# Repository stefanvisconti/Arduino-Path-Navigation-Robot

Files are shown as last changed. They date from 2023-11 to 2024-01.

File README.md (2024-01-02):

# SIngle-Actuator-Arduino-Path-Navigation-Robot
Wheeled Mobile Robot controlled with an Arduino UNO to navigate through pre-determined paths, and around obstacles. A figure of the robot design can be seen below.



The goal of this project is to gain hands-on experience with microcontrollers, sensors, actuators and the programming required to interface with them. The robot is designed to complete four distinct tasks wherein it must: navigate through HMI, navigate autonomously and avoid objects. The solution created was a single actuator design that is able to turn and move forward/backward using one motor on a pivoting ratchet. The robot is able to determine  position using ultrasonic sensors and using these will navigate the tasks accordingly. There are many constraints on this project such as: time, funds and resources which increased the difficulty in creating a solution. In this experiment the design process including: problem definition, solution formulation, modelling, prototyping and implementation will be explored in order to gain in-depth hands-on experience with mechatronics topics.

A video of the system performing in it's manual control option is shown below.

https://drive.google.com/file/d/11_2gsuO4MDafjLckb3ffVChpPL_l2O8q/view?usp=drive_link

## List of Materials

In order to construct the physical mechanism to be used for this project, mostly 3D printed parts were used for structural elements. The single actuator used is the N20 Motor which was already owned by a group member. The paper clips, copper tubing, and o-rings were scrap materials found at home. All of the remaining electrical parts have been taken from the Elegoo Starter Kit. However, a complete list of the costs were considered if each component needed to be purchased. A comprehensive list of all of the hardware that has been used in this project is given in the table below.

<table>
  <tr>
    <th>Name</th>
    <th>Description</th>
    <th>Quantity</th>
    <th>Unit Cost</th>
    <th>Cost</th>
  </tr>
  <tr>
    <td>Main Body Back</td>
    <td>3D Printed</td>
    <td>1</td>
    <td>$0</td>
    <td>$0</td>
  </tr>
  <tr>
    <td>Back Deck</td>
    <td>3D Printed</td>
    <td>1</td>
    <td>$0</td>
    <td>$0</td>
  </tr>
  <tr>
    <td>Back Wheel</td>
    <td>3D Printed</td>
    <td>2</td>
    <td>$0</td>
    <td>$0</td>
  </tr>
  <tr>
    <td>Back Wheel Axle</td>
    <td>3D Printed</td>
    <td>2</td>
    <td>$0</td>
    <td>$0</td>
  </tr>
  <tr>
    <td>Ring Gear Plate</td>
    <td>3D Printed</td>
    <td>1</td>
    <td>$0</td>
    <td>$0</td>
  </tr>
  <tr>
    <td>Main Pivot</td>
    <td>3D Printed</td>
    <td>1</td>
    <td>$0</td>
    <td>$0</td>
  </tr>
  <tr>
    <td>Motor Frame</td>
    <td>3D Printed</td>
    <td>1</td>
    <td>$0</td>
    <td>$0</td>
  </tr>
  <tr>
    <td>Main Wheel Gear</td>
    <td>3D Printed</td>
    <td>1</td>
    <td>$0</td>
    <td>$0</td>
  </tr>
  <tr>
    <td>Idler Gear</td>
    <td>3D Printed</td>
    <td>1</td>
    <td>$0</td>
    <td>$0</td>
  </tr>
  <tr>
    <td>Spur Gear</td>
    <td>3D Printed</td>
    <td>1</td>
    <td>$0</td>
    <td>$0</td>
  </tr>
  <tr>
    <td>Motor Gear</td>
    <td>3D Printed</td>
    <td>1</td>
    <td>$0</td>
    <td>$0</td>
  </tr>
  <tr>
    <td>Bevel Gear</td>
    <td>3D Printed</td>
    <td>1</td>
    <td>$0</td>
    <td>$0</td>
  </tr>
  <tr>
    <td>Bevel Spur Gear</td>
    <td>3D Printed</td>
    <td>1</td>
    <td>$0</td>
    <td>$0</td>
  </tr>
  <tr>
    <td>Idler</td>
    <td>3D Printed</td>
    <td>1</td>
    <td>$0</td>
    <td>$0</td>
  </tr>
  <tr>
    <td>Pivot Cap</td>
    <td>3D Printed</td>
    <td>1</td>
    <td>$0</td>
    <td>$0</td>
  </tr>
  <tr>
    <td>Brush Mount</td>
    <td>3D Printed</td>
    <td>1</td>
    <td>$0</td>
    <td>$0</td>
  </tr>
  <tr>
    <td>Brush Mount Clamp</td>
    <td>3D Printed</td>
    <td>1</td>
    <td>$0</td>
    <td>$0</td>
  </tr>
  <tr>
    <td>Elegoo UNO R3</td>
    <td>Elegoo Starter Kit</td>
    <td>1</td>
    <td>$23.99</td>
    <td>$23.99</td>
  </tr>
  <tr>
    <td>L298N Motor Driver</td>
    <td>Elegoo Starter Kit</td>
    <td>1</td>
    <td>$3.95</td>
    <td>$3.95</td>
  </tr>
  <tr>
    <td>MPU6050 IMU Sensor</td>
    <td>Elegoo Starter Kit</td>
    <td>1</td>
    <td>$7.50</td>
    <td>$7.50</td>
  </tr>
  <tr>
    <td>HC-SR04 Ultrasonic Sensor</td>
    <td>Elegoo Starter Kit</td>
    <td>2</td>
    <td>$4.50</td>
    <td>$9.00</td>
  </tr>
  <tr>
    <td>N20 DC Motor</td>
    <td>Elegoo Starter Kit</td>
    <td>1</td>
    <td>$7.99</td>
    <td>$7.99</td>
  </tr>
  <tr>
    <td>Copper Tubing</td>
    <td>Scrap Material</td>
    <td>1</td>
    <td>$1.20</td>
    <td>$1.20</td>
  </tr>
  <tr>
    <td>Paper Clip</td>
    <td>Scrap Material</td>
    <td>2</td>
    <td>$0.10</td>
    <td>$0.20</td>
  </tr>
  <tr>
    <td>O-Ring</td>
    <td>Scrap Material</td>
    <td>4</td>
    <td>$1.36</td>
    <td>$5.44</td>
  </tr>
  <tr>
    <td>9V Battery</td>
    <td>Elegoo Starter Kit</td>
    <td>1</td>
    <td>$4.50</td>
    <td>$4.50</td>
  </tr>
  <tr>
    <td>Spring</td>
    <td>Scrap Material</td>
    <td>1</td>
    <td>$1.20</td>
    <td>$1.20</td>
  </tr>
  <tr>
    <td>4x3/4 Countersink Screw</td>
    <td>Scrap Material</td>
    <td>6</td>
    <td>$0.67</td>
    <td>$4.00</td>
  </tr>
  <tr>
    <td>M3 Screw</td>
    <td>Scrap Material</td>
    <td>4</td>
    <td>$0.60</td>
    <td>$2.40</td>
  </tr>
  <tr>
    <td>Wire</td>
    <td>Elegoo Starter Kit</td>
    <td>23</td>
    <td>$0.56</td>
    <td>$12.99</td>
  </tr>
  <tr>
    <td>PKCELL 9V Battery Connector</td>
    <td>Elegoo Starter Kit</td>
    <td>1</td>
    <td>$5.33</td>
    <td>$5.33</td>
  </tr>
  <tr>
    <td>Total Cost</td>
    <td></td>
    <td></td>
    <td></td>
    <td>$89.69</td>
  </tr>
</table>

## Schematic and Technical Design Details of Electronics

A circuit diagram of this hardware setup can be seen below. This is created digitally using the TinkerCAD software offered by Autodesk. The diagram is a simplified representation of the wiring setup, where the components are shown graphically. 



However, if a more accurate-to-real-life circuit diagram is desired, an alternative modelling software must be used. The electrical wiring schematic developed using KiCAD can be seen in the figure below. This circuit provides more accuracy, allowing the circuit to be modelled more accurately to the real life thing.



In the figure above, the MPU-6050 symbol is the MPU6050 IMU Sensor board, and the L298N symbol is the L298N Motor Driver board. The Motor_DC symbol is the DC motor being used to drive the gearbox. The two HC-SR04 symbols are the two ultrasonic sensors used for obstacle avoidance in task 3. Finally, the AnalogJoystick1 symbol is the joystick module used to manually control the device. Additionally, the Arduino_UNO_R3 module represents the Elegoo UNO R3 board.

## CAD Models and Technical Design Details of Mechanics

The physical design of this system is quite intricate given the single actuator used to drive the system. Due to this stipulation, certain design considerations must be taken in order to achieve this goal. Additionally, the car was to be constructed using only available materials, and no parts were to be purchased, implying that the cost of the car would be $0. This resulted in almost all of the parts of the device being 3D printed.

The main form of the device is a car with 3 wheels. The two wheels at the back of the car are idler wheels, and are simply there to provide support to the vehicle while it drives. The wheel in the front is the driving wheel, which is fitted with a gearbox and a motor. The front wheel will be able to drive the car forward, as well as rotate to act like a pivot. This is how the car will be able to steer.
The entire mechanism assembly can be seen below, modelled using the online CAD software, Onshape.



The assembly consists of a number of parts. These include the motor, Elegoo UNO R3 board, spring, ultrasonic sensors, o-rings, and all of the 3D printed parts. The 3D printed parts make up the large majority of the assembly. These include, the main body, back deck, back wheel, back wheel axle, ring gear plate, main pivot, motor frame, main wheel gear, idler gear, spur gear, motor gear, bevel gear, bevel spur gear, idler, pivot cap, brush mount, brush mount clamp, ultrasonic sensor mount, and ultrasonic sensor mount mount.

To start, the main body is the largest part of the assembly, all other parts connect to this. It features two cutouts on the side with a threaded hole for the back wheel axle to screw into. It also has the back of the body hollowed out with slots for the back deck to slide into. It also has a circular cutout on the front with screw holes for the ring gear plate with screw holes to screw into. A screenshot of the CAD model of this is shown below.



Sliding into the main body is the back deck. This features a plate for the Elegoo UNO R3 board to screw into. Underneath the back deck is where the L298N motor driver is housed. A screenshot of the CAD model of this is shown below.



Again, attaching to the main body are the back wheel axles. There are two of these and they are fitted with threaded rods that will allow them to screw into the main body. A screenshot of the CAD model of this is shown below.



Accompanying the back wheel axle is the back wheel. This is what provides stability to the rear of the car. They have grooves along the circumference of the wheel in which a plumbing o-ring is able to fit around. This provides the friction needed to be able to spin on the floor. A screenshot of the CAD model of this is shown below.



Another large part of the assembly is the ring gear plate. This screws into the front of the main body and features a large ring gear which will allow the front wheel to pivot around. A screenshot of the CAD model of this is shown below.



The Elegoo UNO R3 board is the main brains of the device. This controls the motor speed and direction and reads and processes values from the sensors. A screenshot of the CAD model of this is shown below.



Sliding through the top of the ring gear plate is the main pivot. This part will be rotating with the main wheel. It is fastened to the ring gear using a set of nuts. The main pivot will also have a hole cut through the middle of it to allow the wires from the motor to be snaked through to be accessible by the arduino. Additionally, with the wires, the pivot will support two pieces of brass tubing which will be used as commutator wings. The wires will be soldered to these and have brushes (paperclips) which will allow power to be supplied to the motor without having the wires get tangled as it rotates. A screenshot of the CAD model of this is shown below.



The brushes, which in this case are paper clips, will be fastened to the device using the brush mounts. These will be screwed into the ring gear plate, and will act as a clamp on the paper clips. One end of the paper clip will be brushing the commutator rings, and the other end will be soldered to a wire which is connected to the L298N motor driver. A screenshot of the CAD model of these are shown below.



Attached to the main pivot is the motor frame. This is quite the complex part as it will the motor and all of the gears which will allow the single actuator steering mechanism to work. A screenshot of the CAD model of this is shown below.



The main wheel of the car features a 38 tooth gear which will be driven by the gearbox on the motor frame. Similarly to the back wheel, it will also have two plumbing o-rings around it which will provide the friction needed for it to drive on the floor. A screenshot of the CAD model of this is shown below.



Next are the rest of the gears. The majority of these look quite similar. A screenshot of the CAD model of all of these are shown below.



Accompanying the gears is the idler. This is the main part that will allow for the single actuator steering mechanism to work. It allows the idler gear to switch between meshing with the main wheel gear and meshing with the pivot mechanism. When the motor changes direction, a spring pushing on the idler allows the idler to switch between driving mechanisms. However, it applies just enough force to allow the idler to move but not enough for the motor gear to be prevented from turning. A screenshot of the CAD model of this is shown below.



A screenshot of the overall driving mechanism can be seen below.



The sensing of the device is done using ultrasonic sensors which are mounted to the front of the car. This sensor mount comes in two pieces. One large piece which will attach onto the ring gear plate, and another which will hold the ultrasonic sensor. These two pieces will screw into each other. It was decided that the necessary distance between each sensor would be 3 inches. A screenshot of the CAD model of these are shown below.



## Controller Design and Block Diagram of Control System

The control system of this project is designed based on the mathematical modelling and simulation previously done. This was the result of the inverse kinematics problem, and the Simulink simulation of the system. From the equations developed in that section, the block diagram for the control system can be created. The controller itself will be described by a transfer function which will be created from the equations previously obtained.
The control system for this project can be described using the following block diagram shown below.



The Ts block represents the transfer function developed in the Mathematical Modelling section. The vRs block represents the desired robot velocity, s represents the wheel angular velocities, t represents the current angle of the robot. The controller takes in the desired velocity of the robot, and outputs the corresponding wheel angular velocities that will achieve that velocity.

## Flowchart and Description of the Software Program

The flowcharts that describe the Arduino scripts can be found in the following figures. All scripts begin by including the necessary libraries, assigning respective pins for sensors and motor, defining all required variables and setting the pin modes. For manual control, the void loop() consists of reading the joystick data and mapping the joystick position to motor speed. That is, for the joystick range of 0 to 1023, the motor speed is mapped from -255 to 255. If the joystick is in the forward position (i.e, positive motor speed), then the motor drives the robot forward. Simularily, if the joystick is in the backward direction (i.e., negative motor speed), then the motor is reversed resulting in the rotation of the steering shaft. If neither statement is true, then the motor stops and the robot does not move. The flowchart for manual control can be seen below. 



For autonomous path navigation, the void loop() begins by reading the ultrasonic and MPU data. The ultrasonic is used to detect the distance of objects ahead, while the MPU measures the rotation of the steering shaft such that the exact direction is known. If the robot is not close to an object, then the robot continues moving forward. If the robot is close to the first object, then the robot turn right 90-degrees. If the robot is close to the second object, then the robot turns left 90-degrees. If the robot senses an object, but it is neither the first or the second, then the robot is at the final object and motion is stopped. The flowchart for autonomous path navigation can be seen below. 



For obstacle avoidance, the void loop() begins by reading the ultrasonic and MPU data. If the robot is not close to an object, then the robot continues moving forward. If the robot is close to the object, then an avoidance deviation sequence is initiated. That is, the robot turns right and travels forward for X seconds until the object is clear. Then the robot turns left and goes forward for X seconds to get past the object. The robot then turns left again and goes forward for X seconds to reach the original path. Another right turn is executed to face the robot towards the finish line. The robot then travels forward for X seconds until the robot reaches the finish line. The flowchart for obstacle avoidance can be seen below. 



Simularily, for the accuracy test, the void loop() begins by reading the ultrasonic and MPU data. If the robot is not close to an object, then the robot continues moving forward. Each time the robot get close to an object it turns right and continues forward. If the senses object is the forth object, then the script ends. The flowchart for the accuracy test can be seen in the figure below. 



## Conclusions and Recommendations

Overall the robotic system that was created was able to be both mechanically innovative and realistically feasible with its execution of the tasks as detailed by the project addendum. Fundamental design formulas were followed during the conceptualization of the solution put forth in this project. These involved strong project initialization exercises such as mind maps, clearly defined functional, constraints and characteristics, and black box diagrams to be used when coming to the formulation of the design. This came to fruition as a one actuated geared robotic drive system that would be able to drive and pivot with two degrees of freedom. The design was easy to drive and provided comparatively little error as opposed to robots with more actuators. To begin the design process of this both mathematical and simulated models were created to test the feasibility of the design. Afterwards, detailed CADs were created to make a model that was almost completely 3D printed. This had the added benefit of keeping the cost of the robots to 0$ which was another one of the ancillary goals of the project detail. 

To control the robot, Arduino along with an ultrasonic sensor, and MPU 6050 was used to both determine any obstacles or the position of the robot. The MPU was especially important for the bearing of the pivot along with the rotation of the body of the drone. In addition, the motion of the robot was mathematically modelled using inverse kinematics. A transfer function was developed such that the controller takes in the desired velocity of the robot, and outputs the corresponding wheel angular velocities that will achieve that velocity.

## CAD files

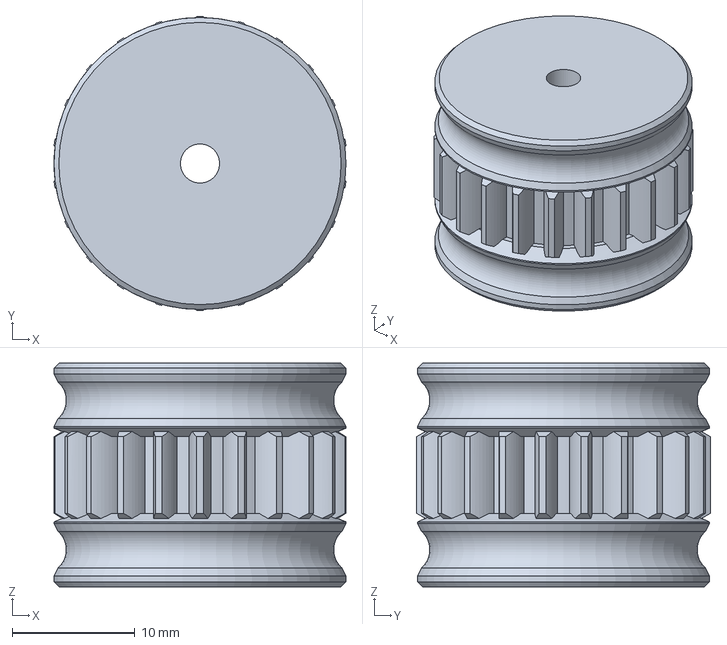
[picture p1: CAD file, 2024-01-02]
CAD Models/Main Wheel Gear.step
23.8 x 24.0 x 18.3 mm

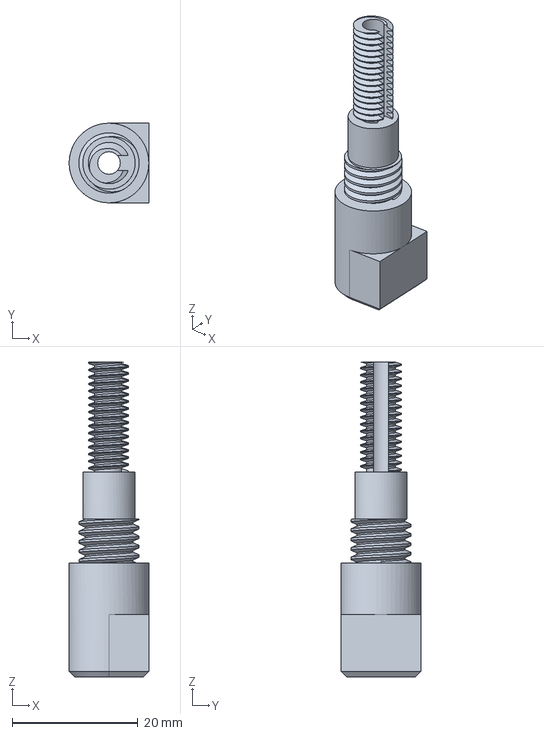
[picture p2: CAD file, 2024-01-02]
CAD Models/Main Pivot.step
12.7 x 12.7 x 50.2 mm

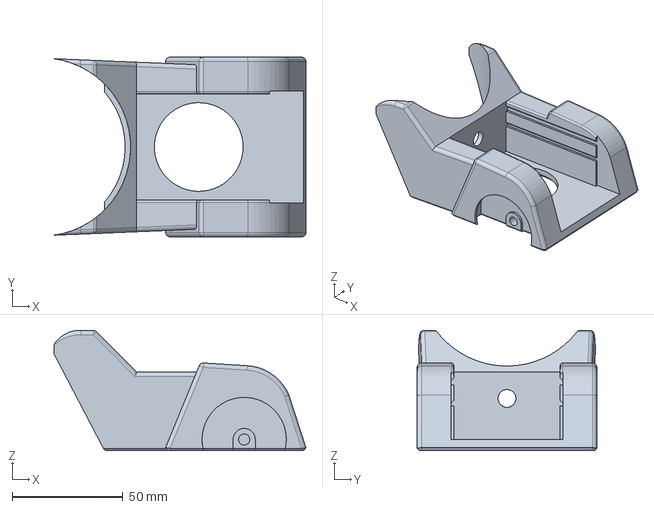
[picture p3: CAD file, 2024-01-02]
CAD Models/Main Body Back.step
113.6 x 81.0 x 54.2 mm

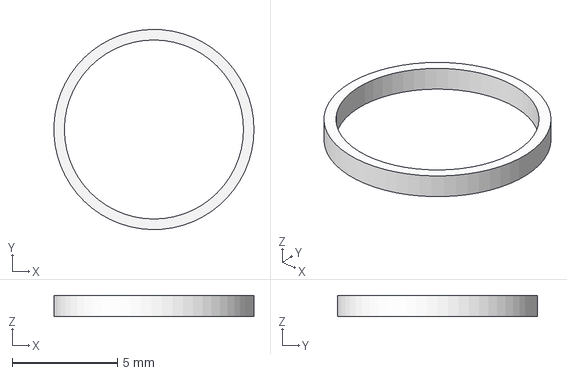
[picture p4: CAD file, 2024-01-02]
CAD Models/Commutator Ring Spacer.step
9.49 x 9.50 x 1.00 mm

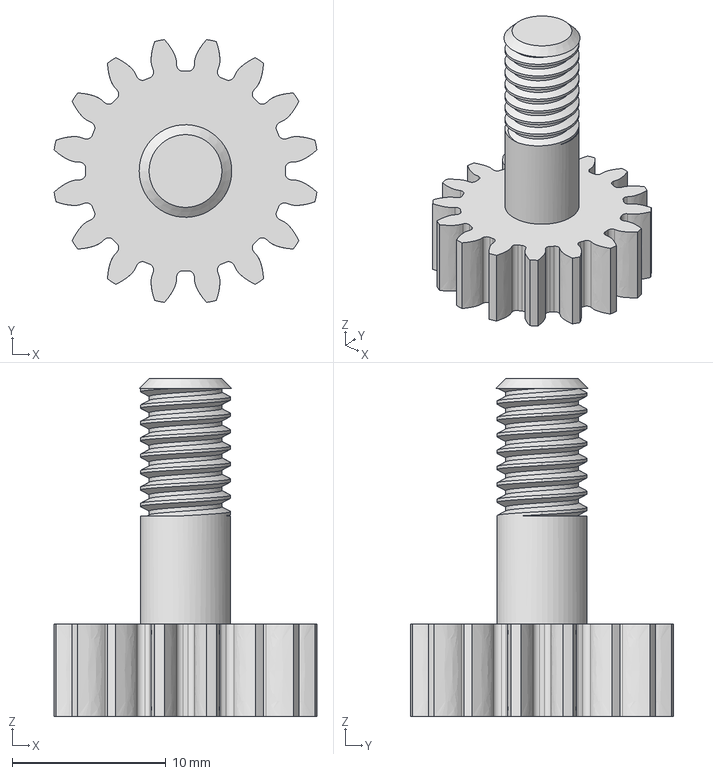
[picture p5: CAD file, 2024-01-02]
CAD Models/Motor Gear.step
17.1 x 17.1 x 22.0 mm

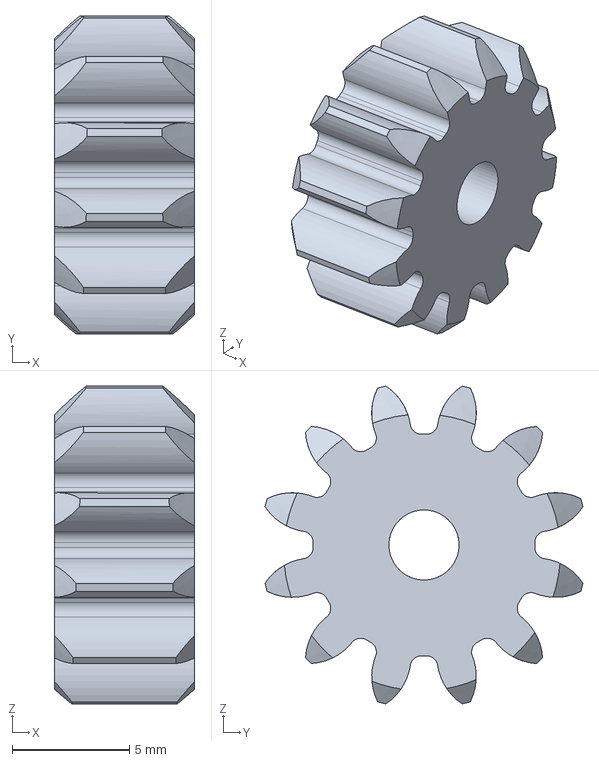
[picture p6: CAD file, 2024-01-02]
CAD Models/Idler Gear.step
6.00 x 13.6 x 13.6 mm

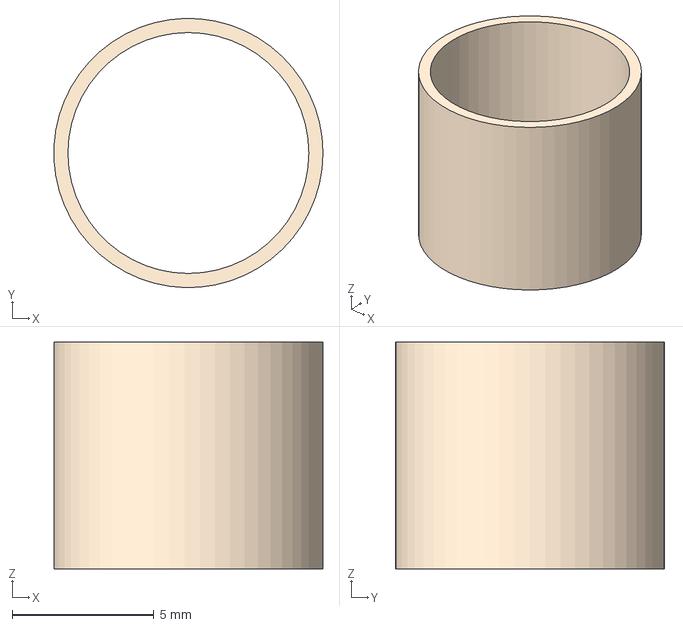
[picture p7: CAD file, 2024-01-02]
CAD Models/Commutator Ring.step
9.49 x 9.50 x 8.00 mm

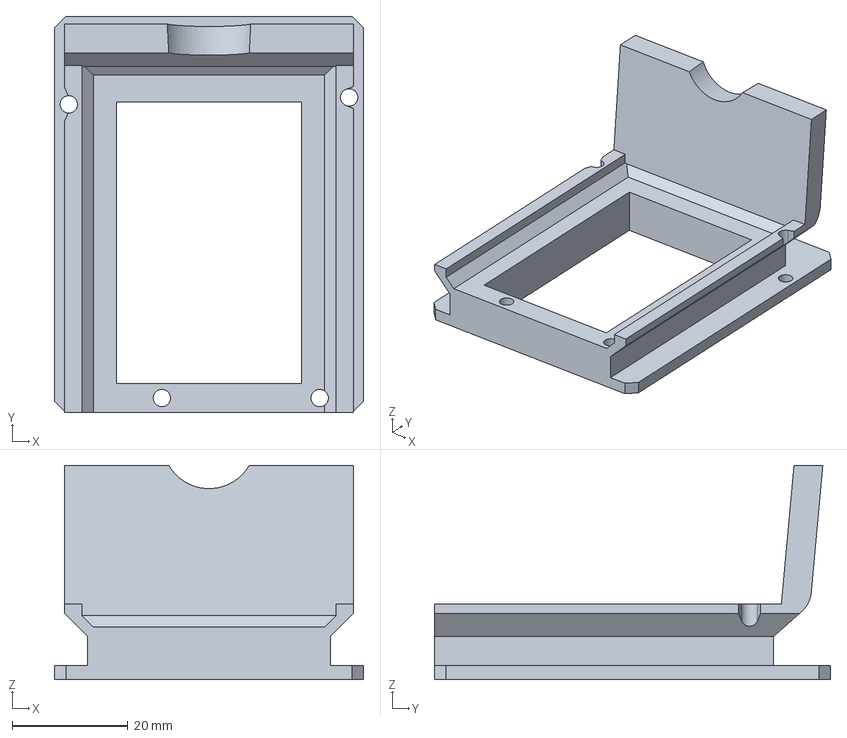
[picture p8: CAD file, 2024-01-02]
CAD Models/Back Deck.step
53.5 x 68.5 x 37.1 mm

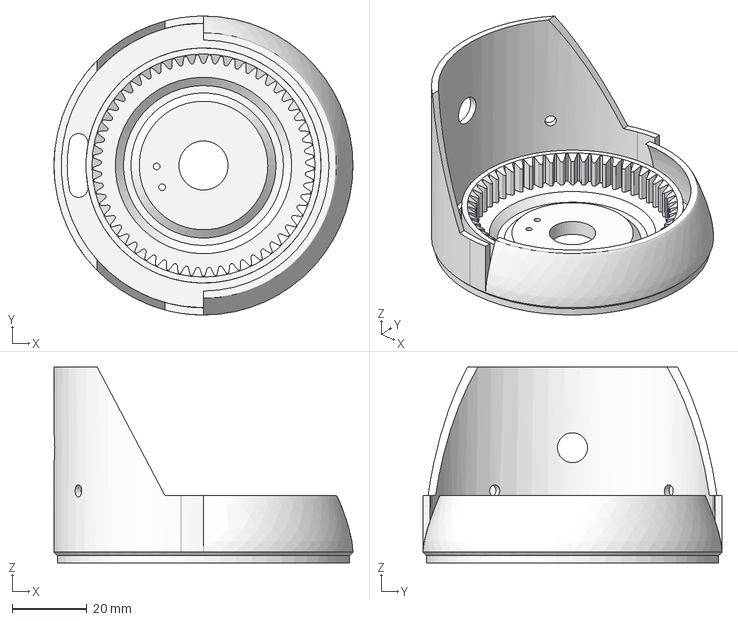
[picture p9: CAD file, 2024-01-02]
CAD Models/Ring Gear Plate.step
79.7 x 79.7 x 52.2 mm

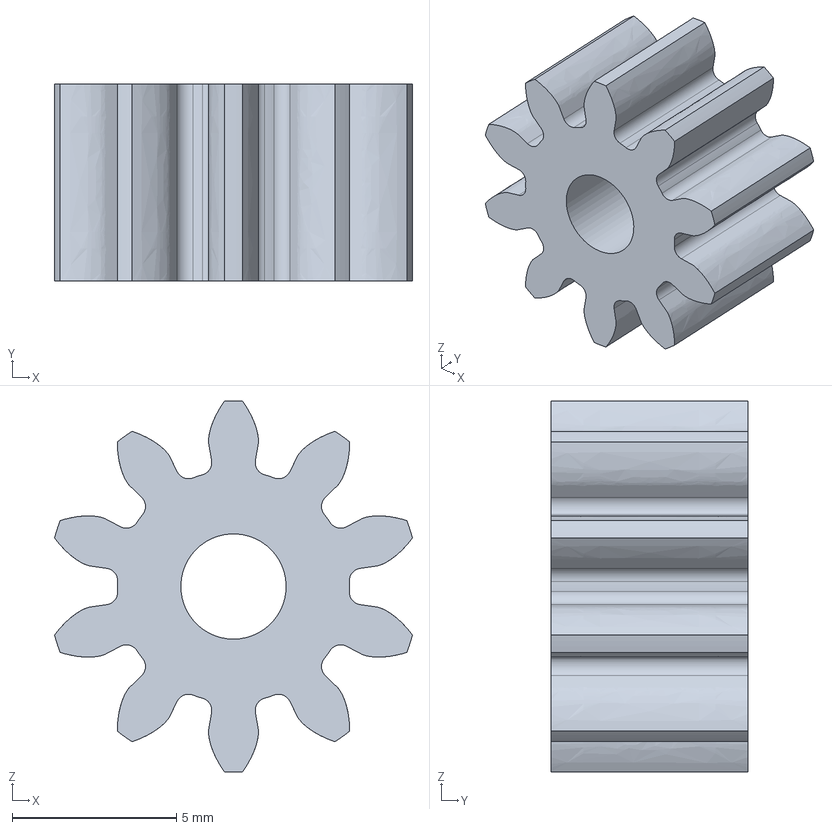
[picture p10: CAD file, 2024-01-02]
CAD Models/Spur Gear.step
10.9 x 6.00 x 11.3 mm

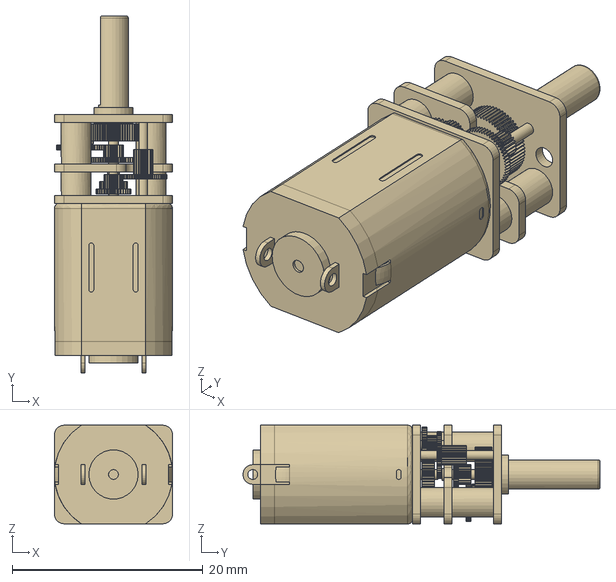
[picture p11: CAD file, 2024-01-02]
CAD Models/N20 DC MOTOR (1).step
12.4 x 37.4 x 10.3 mm

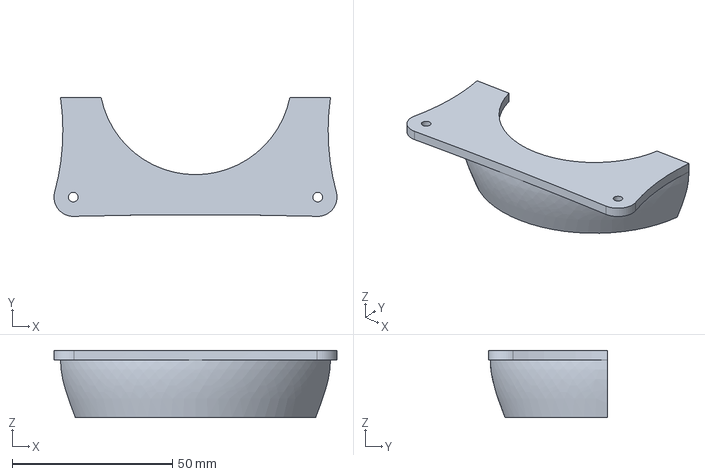
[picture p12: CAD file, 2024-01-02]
CAD Models/Ultrasonic Sensor Mount Mount.step
88.2 x 37.0 x 21.0 mm

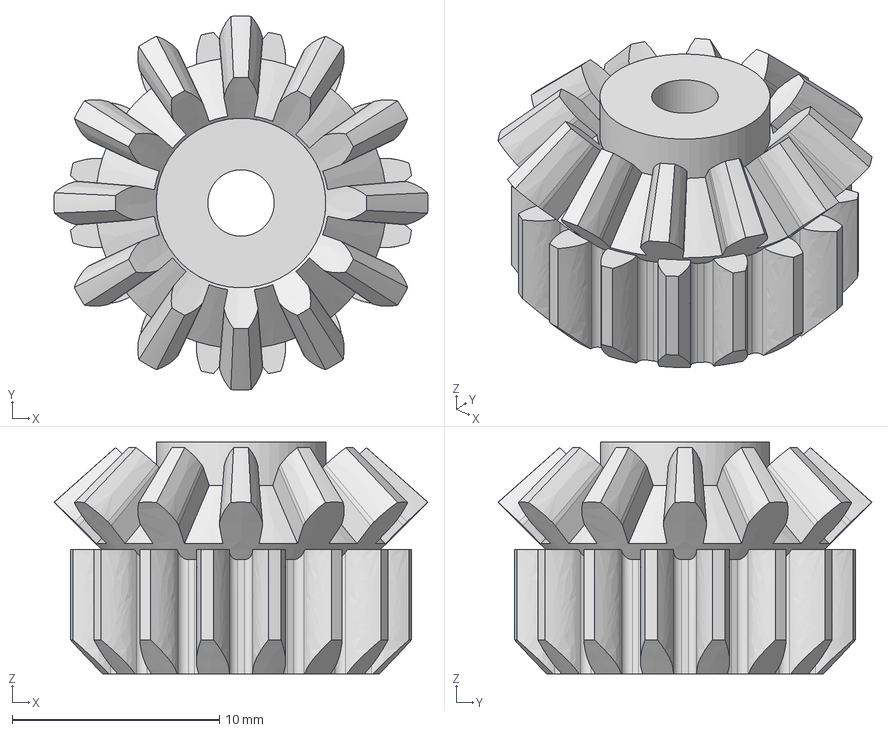
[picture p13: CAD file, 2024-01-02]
CAD Models/Bevel Spur Gear.step
18.0 x 18.0 x 11.2 mm

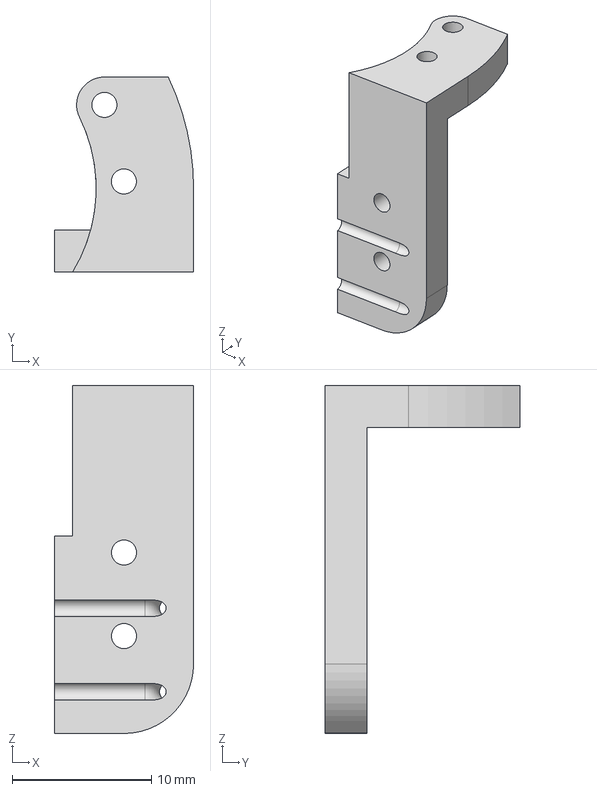
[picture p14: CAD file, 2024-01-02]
CAD Models/Brush Mount.step
10.0 x 14.0 x 25.0 mm

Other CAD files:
CAD Models/hc-sr04 (1).step
CAD Models/Idler.step
CAD Models/Back Wheel.step
CAD Models/Ultrasonic Sensor Mount.step
CAD Models/Arduino-UNO.step
CAD Models/Back Wheel Axle.step
CAD Models/Bevel Gear.step
CAD Models/Brush Mount Clamp.step
CAD Models/Motor Frame.step
CAD Models/Paper Clip.step
CAD Models/Pivot Cap.step

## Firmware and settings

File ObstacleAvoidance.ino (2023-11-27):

#include <Wire.h>
#include <HCSR04.h>

// Rotary Encoder Inputs
#define Clock 10  //Clock pin connected to D9
#define Data 11   //Data pin connected to D8

int counter = 0;         //Use this variable to store "steps"
int currentStateClock;   //Store the status of the clock pin (HIGH or LOW)
int lastStateClock;      //Store the PREVIOUS status of the clock pin (HIGH or LOW)
String currentDir = "";  //Use this to print text
int angleR = 0;

const int trigPin = 2;
const int echoPin = 3;

long duration;  // Time taken for the ultrasonic pulse to travel to the object and back
int distance;   // Calculated distance in centimeters

int m = 0;
int q = 1;
int r = 0;
int s = 0;
int i = 0;
int p = 0;

const int MPU = 0x68;                                            // MPU6050 I2C address
float AccX, AccY, AccZ;                                          //linear acceleration
float GyroX, GyroY, GyroZ;                                       //angular velocity
float accAngleX, accAngleY, gyroAngleX, gyroAngleY, gyroAngleZ;  //used in void loop()
float roll, pitch, yaw;
float AccErrorX, AccErrorY, GyroErrorX, GyroErrorY, GyroErrorZ;
float elapsedTime, currentTime, previousTime;
int c = 0;

int angle;  //due to how I orientated my MPU6050 on my car, angle = roll
float targetAngle = 0;

// Motor control pins for L298N
const int enablePin = 9;  // Enable pin of the L298N motor driver
const int in1 = 8;        // IN1 pin of the L298N motor driver
const int in2 = 7;        // IN2 pin of the L298N motor driver

// Constants for motor control
const int motorSpeed = 255;  // Adjust this value based on your motor and robot characteristics

void setup() {
  Serial.begin(9600);
  Wire.begin();                 // Initialize comunication
  Wire.beginTransmission(MPU);  // Start communication with MPU6050 // MPU=0x68
  Wire.write(0x6B);             // Talk to the register 6B
  Wire.write(0x00);             // Make reset - place a 0 into the 6B register
  Wire.endTransmission(true);   //end the transmission
  // Call this function if you need to get the IMU error values for your module
  calculateError();
  delay(20);
  currentTime = micros();
  pinMode(enablePin, OUTPUT);
  pinMode(in1, OUTPUT);
  pinMode(in2, OUTPUT);
  pinMode(trigPin, OUTPUT);
  pinMode(echoPin, INPUT);
  delay(1000);

  /*  Set encoder pins as inputs with pullups. If you use the Encoder Module, you don't need
   *  pullups for Clock and Data, only for the push button.*/
  pinMode(Clock, INPUT_PULLUP);
  pinMode(Data, INPUT_PULLUP);

  // Setup Serial Monitor
  Serial.begin(9600);

  // Read the initial state of Clock pin (it could be HIGH or LOW)
  lastStateClock = digitalRead(Clock);
}

void loop() {
  // === Read accelerometer (on the MPU6050) data === //
  readAcceleration();
  // Calculating Roll and Pitch from the accelerometer data
  accAngleX = (atan(AccY / sqrt(pow(AccX, 2) + pow(AccZ, 2))) * 180 / PI) - AccErrorX;  //AccErrorX is calculated in the calculateError() function
  accAngleY = (atan(-1 * AccX / sqrt(pow(AccY, 2) + pow(AccZ, 2))) * 180 / PI) - AccErrorY;

  // === Read gyroscope (on the MPU6050) data === //
  previousTime = currentTime;
  currentTime = micros();
  elapsedTime = (currentTime - previousTime) / 1000000;  // Divide by 1000 to get seconds
  readGyro();
  // Correct the outputs with the calculated error values
  GyroX -= GyroErrorX;  //GyroErrorX is calculated in the calculateError() function
  GyroY -= GyroErrorY;
  GyroZ -= GyroErrorZ;
  // Currently the raw values are in degrees per seconds, deg/s, so we need to multiply by sendonds (s) to get the angle in degrees
  gyroAngleX += GyroX * elapsedTime;  // deg/s * s = deg
  gyroAngleY += GyroY * elapsedTime;
  yaw += GyroZ * elapsedTime;
  //combine accelerometer- and gyro-estimated angle values. 0.96 and 0.04 values are determined through trial and error by other people
  roll = 0.96 * gyroAngleX + 0.04 * accAngleX;
  pitch = 0.96 * gyroAngleY + 0.04 * accAngleY;
  angle = yaw;  //if you mounted MPU6050 in a different orientation to me, angle may not = roll. It can roll, pitch, yaw or minus version of the three
                //for me, turning right reduces angle. Turning left increases angle.

  // Print the values on the serial monitor
  angle = -angle;

  // Trigger the sensor by sending a 10-microsecond pulse
  digitalWrite(trigPin, LOW);
  delayMicroseconds(2);
  digitalWrite(trigPin, HIGH);
  delayMicroseconds(10);
  digitalWrite(trigPin, LOW);
  rotaryMeasure();

  // Read the duration of the pulse from the echo pin
  duration = pulseIn(echoPin, HIGH);


  // Calculate distance in centimeters using the speed of sound (343 meters/second)
  distance = duration * 0.0343 / 2;

  Serial.print("angle: ");
  Serial.print(angle);
  Serial.print(" distance: ");
  Serial.print(distance);
  Serial.print(" M: ");
  Serial.print(m);
  Serial.print(" I: ");  //estimates time to run void loop() once
  Serial.println(i);
  Serial.print(" | AngleR: ");
  Serial.print(angleR);

  if ((distance > 10) && (m == 0)) {
    driveForward();
  } else {
    if ((q == 1)) {

      i = turnRight1(i);
    }
    if (q == 2) {
      i = turnRight2(i);
    }
    if ((q == 3) && (i > 1)) {
      i = turnRight3(i);
    }
    if ((q == 4) && (i > 2)) {
      calculateError();
      Serial.println("WOOHOOO FUCK YEAH!!!!!");
      m = 0;
      q = 1;
      i = 0;
      p = 1;
    }
    if ((m == 0) && (p == 1)) {
      driveForward1();
      delay(7000);
    }
  }
}
void rotaryMeasure() {

  // Read the current state of CLK
  currentStateClock = digitalRead(Clock);

  // If last and current state of Clock are different, then "pulse occurred"
  // React to only 1 state change to avoid double count
  if (currentStateClock != lastStateClock && currentStateClock == 1) {

    // If the Data state is different than the Clock state then
    // the encoder is rotating "CCW" so we decrement
    if (digitalRead(Data) != currentStateClock) {
      counter--;
      currentDir = "Counterclockwise";
    } else {
      // Encoder is rotating CW so increment
      counter++;
      currentDir = "Clockwise";
    }
    angleR = counter * 18;
  }
  if (counter > 19) {
    counter = 0;
  }
  // We save last Clock state for next loop
  lastStateClock = currentStateClock;

  // Read the button state

  // Put in a slight delay to help debounce the reading
  delay(1);
}
//////////////////////////////////////////////////////////////////////////////////////////////////////////////////////////////
void calculateError() {
  //When this function is called, ensure the car is stationary. See Step 2 for more info

  // Read accelerometer values 200 times
  c = 0;
  while (c < 200) {
    readAcceleration();
    // Sum all readings
    AccErrorX += (atan((AccY) / sqrt(pow((AccX), 2) + pow((AccZ), 2))) * 180 / PI);
    AccErrorY += (atan(-1 * (AccX) / sqrt(pow((AccY), 2) + pow((AccZ), 2))) * 180 / PI);
    c++;
  }
  //Divide the sum by 200 to get the error value, since expected value of reading is zero
  AccErrorX = AccErrorX / 200;
  AccErrorY = AccErrorY / 200;
  c = 0;

  // Read gyro values 200 times
  while (c < 200) {
    readGyro();
    // Sum all readings
    GyroErrorX += GyroX;
    GyroErrorY += GyroY;
    GyroErrorZ += GyroZ;
    c++;
  }
  //Divide the sum by 200 to get the error value
  GyroErrorX = GyroErrorX / 200;
  GyroErrorY = GyroErrorY / 200;
  GyroErrorZ = GyroErrorZ / 200;
  Serial.println("The the gryoscope setting in MPU6050 has been calibrated");
}

void readAcceleration() {
  Wire.beginTransmission(MPU);
  Wire.write(0x3B);  // Start with register 0x3B (ACCEL_XOUT_H)
  Wire.endTransmission(false);
  Wire.requestFrom(MPU, 6, true);  // Read 6 registers total, each axis value is stored in 2 registers
  //For a range of +-2g, we need to divide the raw values by 16384, according to the MPU6050 datasheet
  AccX = (Wire.read() << 8 | Wire.read()) / 16384.0;  // X-axis value
  AccY = (Wire.read() << 8 | Wire.read()) / 16384.0;  // Y-axis value
  AccZ = (Wire.read() << 8 | Wire.read()) / 16384.0;  // Z-axis value
}

void readGyro() {
  Wire.beginTransmission(MPU);
  Wire.write(0x43);
  Wire.endTransmission(false);
  Wire.requestFrom(MPU, 6, true);
  GyroX = (Wire.read() << 8 | Wire.read()) / 131.0;
  GyroY = (Wire.read() << 8 | Wire.read()) / 131.0;
  GyroZ = (Wire.read() << 8 | Wire.read()) / 131.0;
}

void driveForward() {
  digitalWrite(in1, LOW);
  digitalWrite(in2, HIGH);
  analogWrite(enablePin, motorSpeed);
}

int driveForward1(p) {
  digitalWrite(in1, LOW);
  digitalWrite(in2, HIGH);
  analogWrite(enablePin, motorSpeed);
}

void driveBackward() {
  rotaryMeasure();
  digitalWrite(in1, HIGH);
  digitalWrite(in2, LOW);
  analogWrite(enablePin, motorSpeed);
}

void Stop() {
  digitalWrite(in1, LOW);
  digitalWrite(in2, LOW);
  analogWrite(enablePin, 0);
}

int turnRight1(int i) {
  if ((angleR < 270)) {
    rotaryMeasure();


    m = 1;
    driveBackward();
    delay(100);
  } else {
    q = 2;
    Stop();
  }
  return i = 1;
}

int turnRight2(int i) {
  if ((angle < 280) && (angle > 170)) {
    rotaryMeasure();


    driveForward();
    m = 2;
    delay(100);
  } else {
    q = 3;
    s = 1;
    r = 0;
    Stop();
  }
  return i = 2;
}

int turnRight3(int i) {
  rotaryMeasure();


  if ((angleR > 0)) {
    driveBackward();
    m = 3;
  } else {
    q = 4;
  }
  return i = 3;
}

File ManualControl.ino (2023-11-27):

//Control Device using Joystick

// Define the pins for the motor driver
const int enablePin = 9;  // Motor driver enable pin (ENA)
const int in1Pin = 7;     // Motor driver input 1 (IN1)
const int in2Pin = 8;     // Motor driver input 2 (IN2)

// Define the joystick pin
const int joystickPinY = A0;

void setup() {

  // Set motor driver pins as OUTPUT
  pinMode(enablePin, OUTPUT);
  pinMode(in1Pin, OUTPUT);
  pinMode(in2Pin, OUTPUT);

  // Initialize the motor as stopped
  digitalWrite(enablePin, LOW);
  digitalWrite(in1Pin, LOW);
  digitalWrite(in2Pin, LOW);
}

void loop() {
  // Read the Y-axis value from the joystick
  int yValue = analogRead(joystickPinY);

  // Map the joystick value to motor speed (adjust the range if needed)
  int motorSpeed = map(yValue, 0, 1023, -255, 255);

  // Control the motor direction based on the joystick value
  if (motorSpeed > 0) {
    // Move forward
    analogWrite(enablePin, abs(motorSpeed));
    digitalWrite(in1Pin, HIGH);
    digitalWrite(in2Pin, LOW);
  } else if (motorSpeed < 0) {
    // Move backward
    analogWrite(enablePin, abs(motorSpeed));
    digitalWrite(in1Pin, LOW);
    digitalWrite(in2Pin, HIGH);
  } else {
    // Stop the motor if the joystick is centered
    digitalWrite(enablePin, LOW);
    digitalWrite(in1Pin, LOW);
    digitalWrite(in2Pin, LOW);
  }
  delay(100);
}
